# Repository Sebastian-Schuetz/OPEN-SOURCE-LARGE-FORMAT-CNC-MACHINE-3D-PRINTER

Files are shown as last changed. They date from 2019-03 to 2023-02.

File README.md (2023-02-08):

# Open-source-Large-CNC

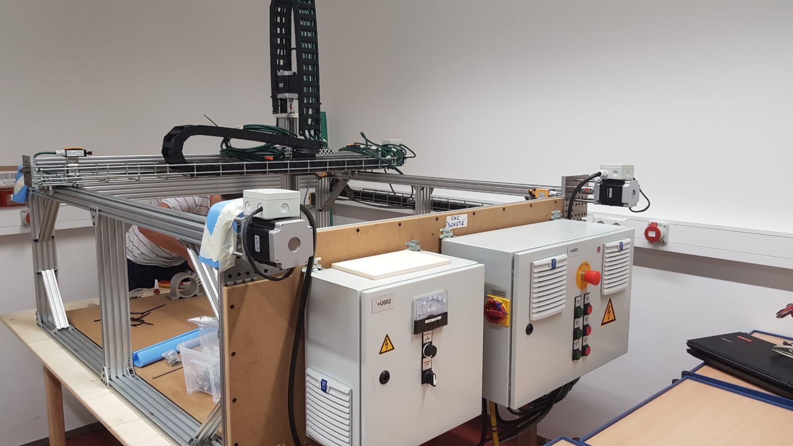
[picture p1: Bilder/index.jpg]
A picture of the finished CNC The finished CNC-machine


In this Github-Repo you can find the Documentation and CAD files for a large format CNC-machine we build with OpenBuilds parts.
This build was also published in the OpenBuilds-Forum: https://openbuilds.com/threads/open-source-large-format-cnc-machine-and-3d-printer.13904/
and on our blog: https://schuetzbuilds.de/open-source-large-format-cnc-machine-and-3d-printer

The total size of the machine is roughly:
-	X: 172 cm
-	Y: 172 cm
-	Z: 128 cm
and weights around 200 kg.

For further information you should take a look in the CNC-OpenBuilds.pdf file! 

Filestructure:

- Bilder: contains (additional) pictures to those in the pdf
- CAD-files: contains CAD-files (who would have thought). Furthermore you can check out the online model here: http://a360.co/2y7nwAO 
- Motormounts-dxf: The 3D-DXF files for the motor mounts, so that you don´t have to extract them form the CAD-model for milling
- Aufbauanleitung.pdf: Contains the "manual" on how to build the CNC. For reference always stick to the CAD.
- CNC-Mill-v3_Render.jpg: A high quality render of the finished machine
- CNC-OpenBuilds.pdf: THE MOST IMPORTANT DOCUMENT. It provides you with further information on the design decisions, ...
- SLP...: The circuit diagram. IT IS 28 PAGES. And was done professionaly. So if you think about building a CNC-machine and want to do it right, this is a great starting point.
- Materialliste.xlsx: The partlist with BOM

As you can see we are still missing some parts for the second y-axis.

# Team
- David Koch
- Sebastian Schütz
- Stefan Schütz

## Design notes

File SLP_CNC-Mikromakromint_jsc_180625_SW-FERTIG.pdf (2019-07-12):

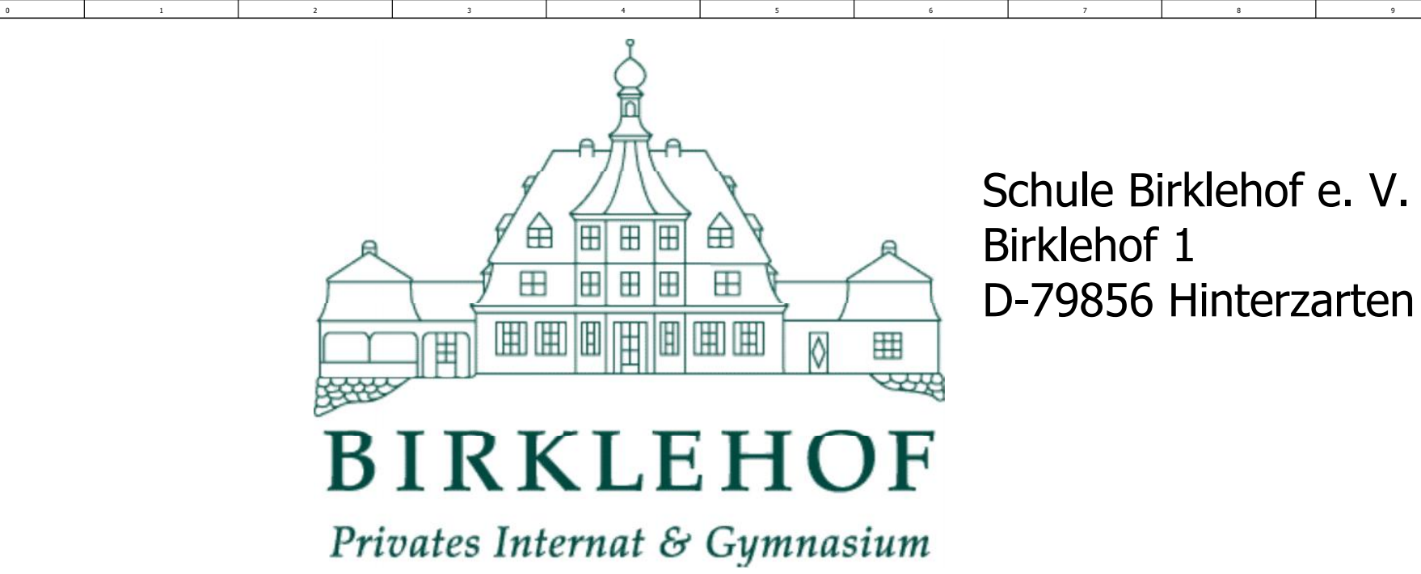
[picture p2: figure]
Schule Birklehof e. V. Birklehof 1 D-79856 Hinterzarten
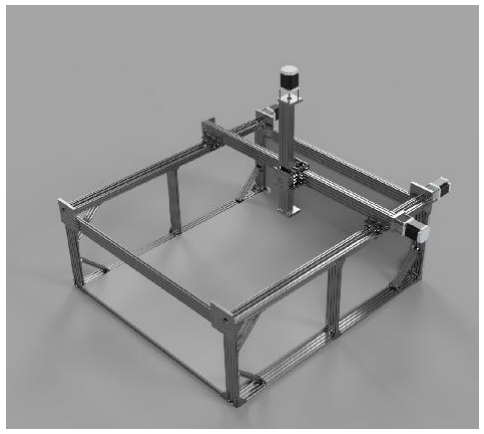
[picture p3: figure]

| | | | 31.01.2018 | 2017/18 CNC-3D-Portalfräse | | Deckblatt | Zeichnungsnummer CNC17-01 | =
| | | Bearb. | schuetz.j | | | | | +
| | | Gepr | | | | | | | Blatt
Änderung | Datum | Name | Urspr | | Ersatz von | Ersetzt durch

&EDA/3

# CNC-3D-Portalfräse

# CNC17-01

# ELEKTRODOKUMENTATION

2017/18

# Projekt: Baujahr:

# Projekt Nr.:

&EDA/4

Urspr | CNC17-01

## Inhaltsverzeichnis

&EDB/3

25.06.2018
Zeichnungsnummer | -600

Fabrik-Nr.

C:\Users\schuetz.j\Daten\Eplan_Prj\CNC-Portalfräse_Mikromakromint.edb\Images\Brunnhuber.jpg | CNC17-01
Seite | Seitenbeschreibung | Seitenzusatzfeld | Datum | Bearbeiter | X
&EAA/1 | Deckblatt | | 31.01.2018 | schuetz.j | X
&EDA/3 | Igus Kette 1+2 | | 12.02.2018 | schuetz.j
&EDA/4 | Igus Kette 3 | | 12.02.2018 | schuetz.j
&EAB/2 | Inhaltsverzeichnis | | 25.06.2018 | schuetz.j
&EDB/3 | Allgemeine Info | | 31.01.2018 | schuetz.j
&EDB/4 | Betriebsmittelkennzeichnung | | 08.02.2018 | schuetz.j
&EFS+U001/1 | Einspeisung | | 22.05.2018 | schuetz.j
&EFS+U001/2 | Steuerung Allgemein | | 22.05.2018 | schuetz.j
&EFS+U001/3 | Steuerung Arduino | | 30.05.2018 | schuetz.j
&EFS+U001/3.a | Arduino Pinout | | 20.02.2018 | schuetz.j
&EFS+U001/4 | Optokoppler - Endschalter | | 25.06.2018 | schuetz.j
&EFS+U001/5 | Optokoppler - Motortreiber | | 25.06.2018 | schuetz.j
&EFS+U001/6 | Leistung X-Achse | | 25.06.2018 | schuetz.j
&EFS+U001/7 | Leistung Y-Achse | | 30.05.2018 | schuetz.j
&EFS+U001/8 | Leistung Z-Achse | | 25.06.2018 | schuetz.j
&EFS+U001/9 | Extruder (optional) | | 25.06.2018 | schuetz.j
&EFS+U002/10 | Frequenzumrichter Spindel | | 22.05.2018 | schuetz.j
&EMB2/24 | Kabelübersicht : =-W0 - =-W504 | | 25.06.2018 | schuetz.j
&EMA1/15 | Klemmenplan +U001-X0 | | 30.05.2018 | schuetz.j
&EMA1/16 | Klemmenplan +U001-X1 | | 25.06.2018 | schuetz.j
&EMA1/17 | Klemmenplan +U001-X2 | | 30.05.2018 | schuetz.j
&EMA1/18 | Klemmenplan +U001-X3 | | 30.05.2018 | schuetz.j
&EMA1/19 | Klemmenplan +U001-X4 | | 25.06.2018 | schuetz.j
&EMA1/20 | Klemmenplan +U001-X4 | | 30.05.2018 | schuetz.j
&EMA1/21 | Klemmenplan +U001-X5 | | 30.05.2018 | schuetz.j
&EMA1/22 | Klemmenplan +U001-X6 | | 25.06.2018 | schuetz.j
&EMA1/23 | Klemmenplan +U002-X5 | | 30.05.2018 | schuetz.j
&EPC/25 | Artikelstückliste : - MEN.Pro Top13A | | 30.05.2018 | schuetz.j
&EPC/26 | Artikelstückliste : Pollin.250411 - Eaton.LS-11/L_#266110 | | 30.05.2018 | schuetz.j
&ETL/30 | Schaltschrankaufbau | | 28.05.2018 | schuetz.j

Spalte X: eine automatisch erzeugte Seite wurde manuell nachbearbeitet

# Inhaltsverzeichnis

F06_001

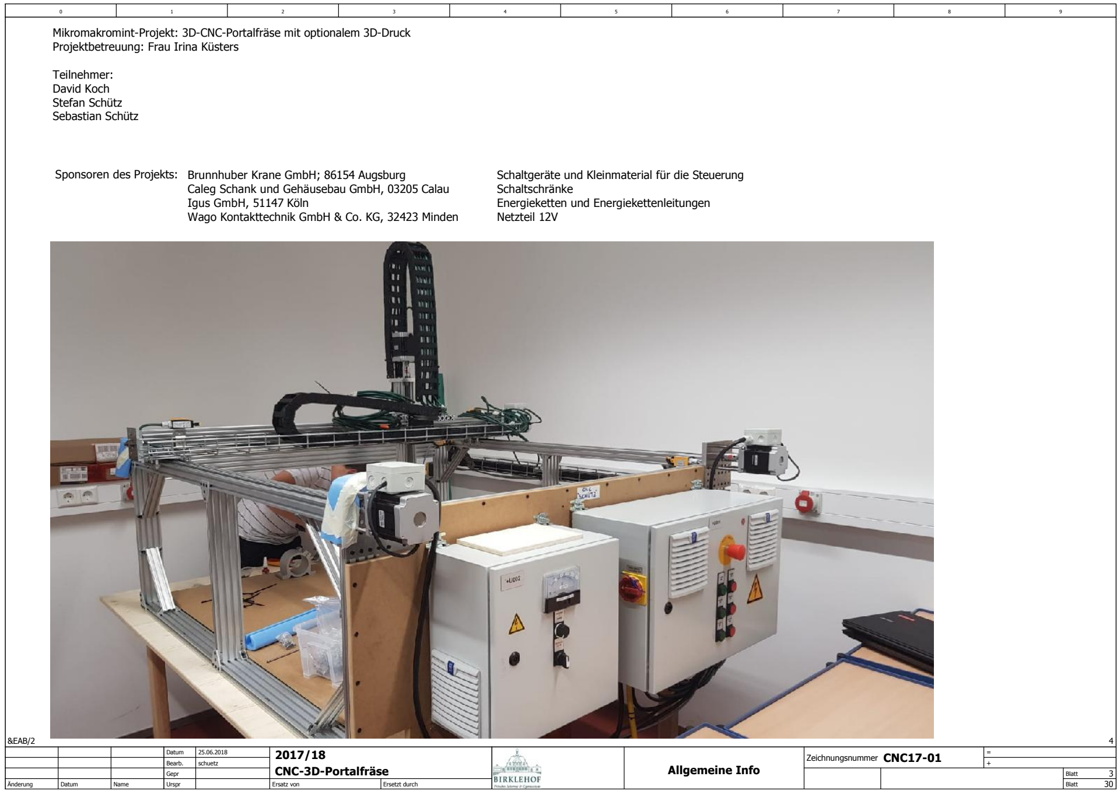
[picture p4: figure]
&EAB/2; schuetz; Allgemeine Info; Projektbetreuung: Frau Irina Küsters; Teilnehmer: David Koch Stefan Schütz Sebastian Schütz; Igus GmbH, 51147 Köln; Schaltschränke; Netzteil 12V

## Mikromakromint-Projekt: 3D-CNC-Portalfräse mit optionalem 3D-Druck

## Sponsoren des Projekts: Brunnhuber Krane GmbH; 86154 Augsburg Caleg Schank und Gehäusebau GmbH, 03205 Calau

## Wago Kontakttechnik GmbH & Co. KG, 32423 Minden

## Schaltgeräte und Kleinmaterial für die Steuerung

## Energieketten und Energiekettenleitungen

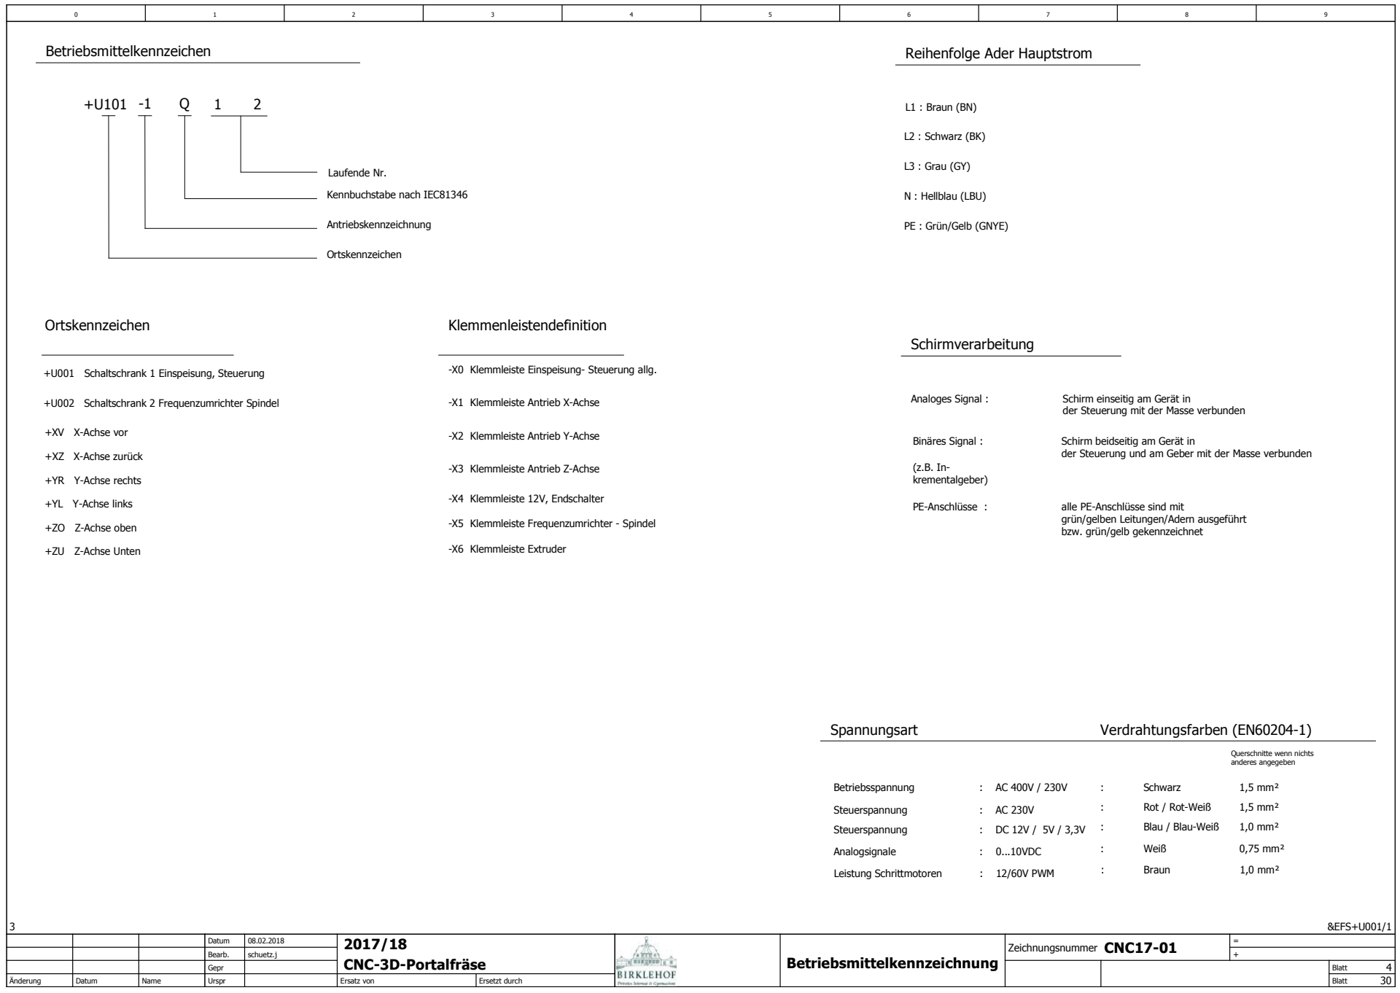
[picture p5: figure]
Betriebsmittelkennzeichnung; &EFS+U001/1; Betriebsmittelkennzeichen; Ortskennzeichen; Kennbuchstabe nach IEC81346; Klemmenleistendefinition; Antriebskennzeichnung; -X2 Klemmleiste Antrieb Y-Achse; -X3 Klemmleiste Antrieb Z-Achse; -X1 Klemmleiste Antrieb X-Achse; -X4 Klemmleiste 12V, Endschalter; Laufende Nr.; +XV X-Achse vor; +XZ X-Achse zurück; +YR Y-Achse rechts; +YL Y-Achse links; +ZO Z-Achse oben; +ZU Z-Achse Unten; -X6 Klemmleiste Extruder; Reihenfolge Ader Hauptstrom; L1 : Braun (BN); L2 : Schwarz (BK); L3 : Grau (GY); N : Hellblau (LBU); Schirmverarbeitung; Analoges Signal :; Binäres Signal :; (z.B. In- krementalgeber); PE-Anschlüsse :; Schirm einseitig am Gerät in der Steuerung mit der Masse verbunden; Schirm beidseitig am Gerät in; alle PE-Anschlüsse sind mit grün/gelben Leitungen/Adern ausgeführt bzw. grün/gelb gekennzeichnet; PE : Grün/Gelb (GNYE); Betriebsspannung; Steuerspannung; Querschnitte wenn nichts anderes angegeben; Schwarz; Rot / Rot-Weiß; Blau / Blau-Weiß; 1,5 mm²; 1,0 mm²

-X0 Klemmleiste Einspeisung- Steuerung allg. +U001 Schaltschrank 1 Einspeisung, Steuerung

+U002 Schaltschrank 2 Frequenzumrichter Spindel

-X5 Klemmleiste Frequenzumrichter - Spindel der Steuerung und am Geber mit der Masse verbunden

Spannungsart | Verdrahtungsfarben (EN60204-1)
Analogsignale | : | Weiß | 0,75 mm² : 0...10VDC
Leistung Schrittmotoren | : | Braun | 1,0 mm² : 12/60V PWM

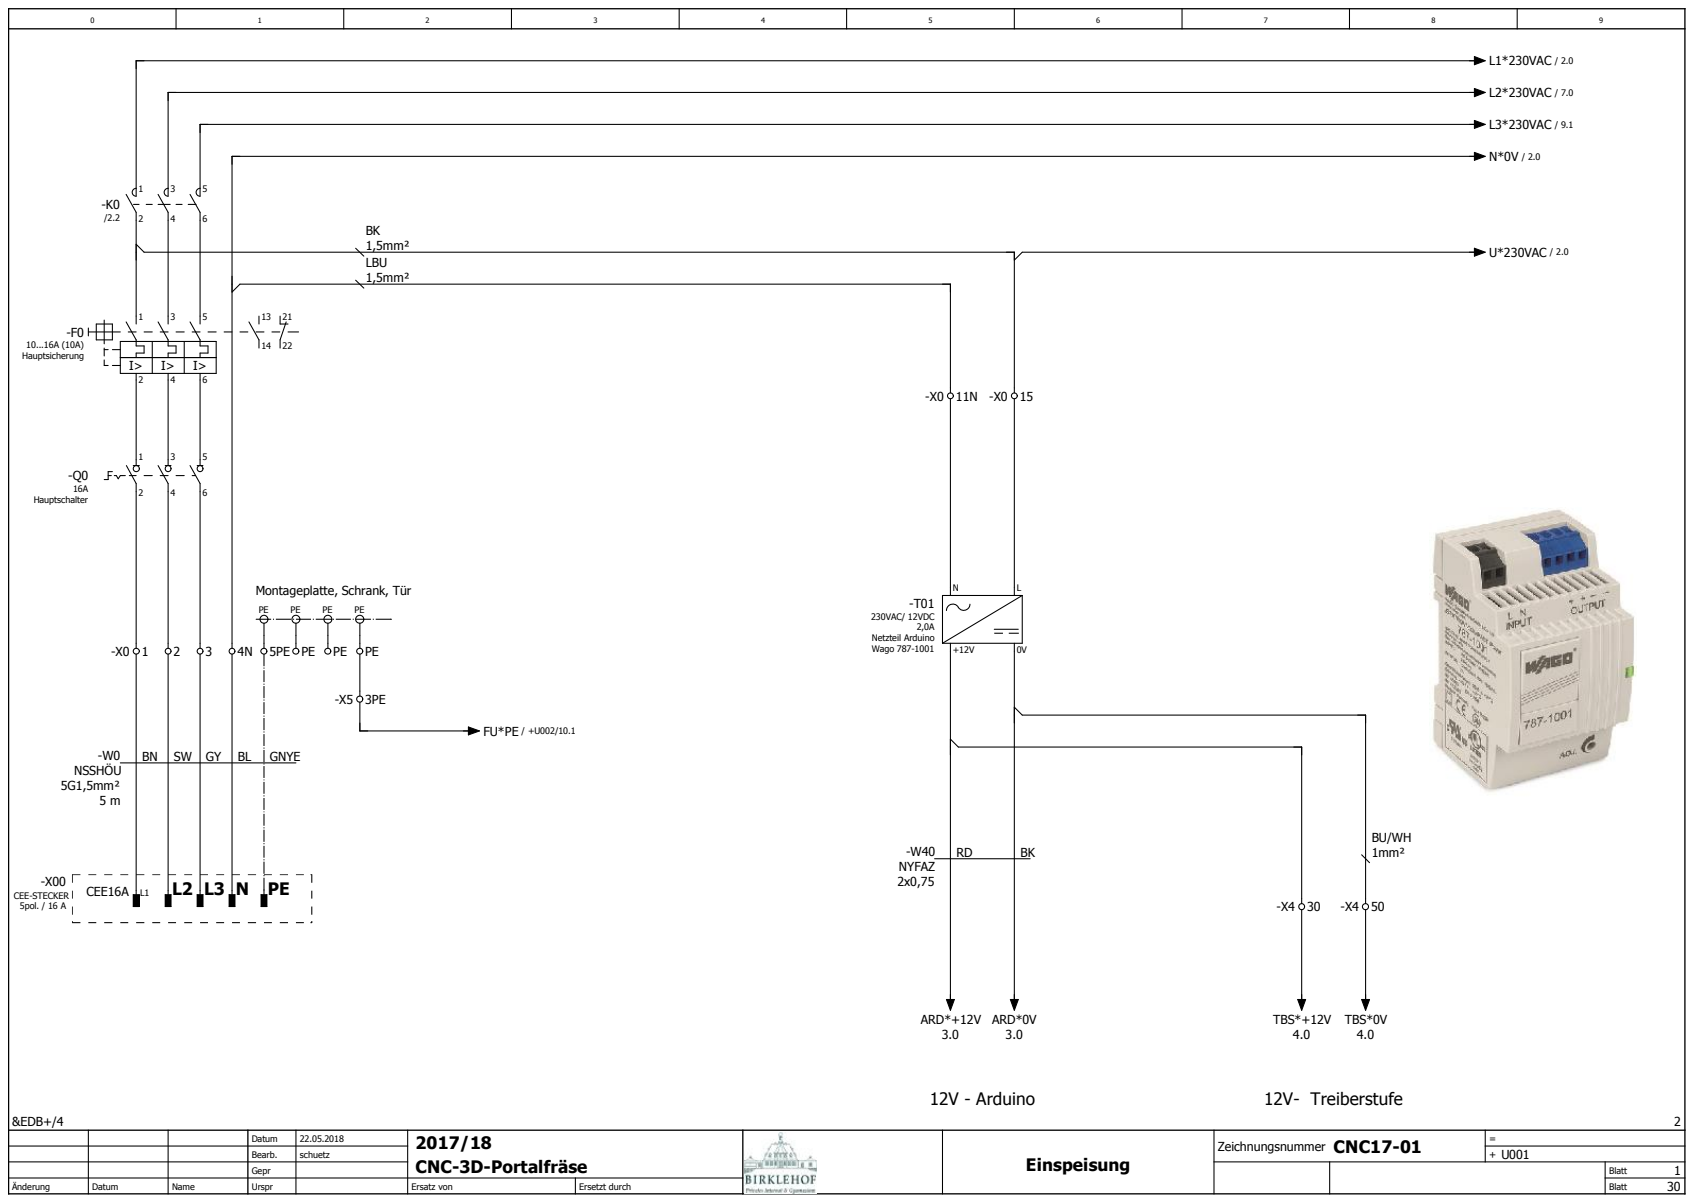
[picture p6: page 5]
&EDB+/4; U001 Einspeisung; 12V - Arduino; 12V- Treiberstufe; -Q0 16A Hauptschalter; -F0 10...16A (10A) Hauptsicherung; CEE16A L1; CEE-STECKER 5pol. / 16 A; NSSHÖU 5G1,5mm² 5 m; BL GNYE; -T01 230VAC/ 12VDC 2,0A Netzteil Arduino Wago 787-1001; 1mm²; 1,5mm²; LBU; -W40 NYFAZ 2x0,75; ARD*+12V 3.0; ARD*0V 3.0; L2*230VAC / 7.0; L1*230VAC / 2.0; L3*230VAC / 9.1; U*230VAC / 2.0; TBS*+12V 4.0; TBS*0V 4.0

Montageplatte, Schrank, Tür

22.05.2018
schuetz | +

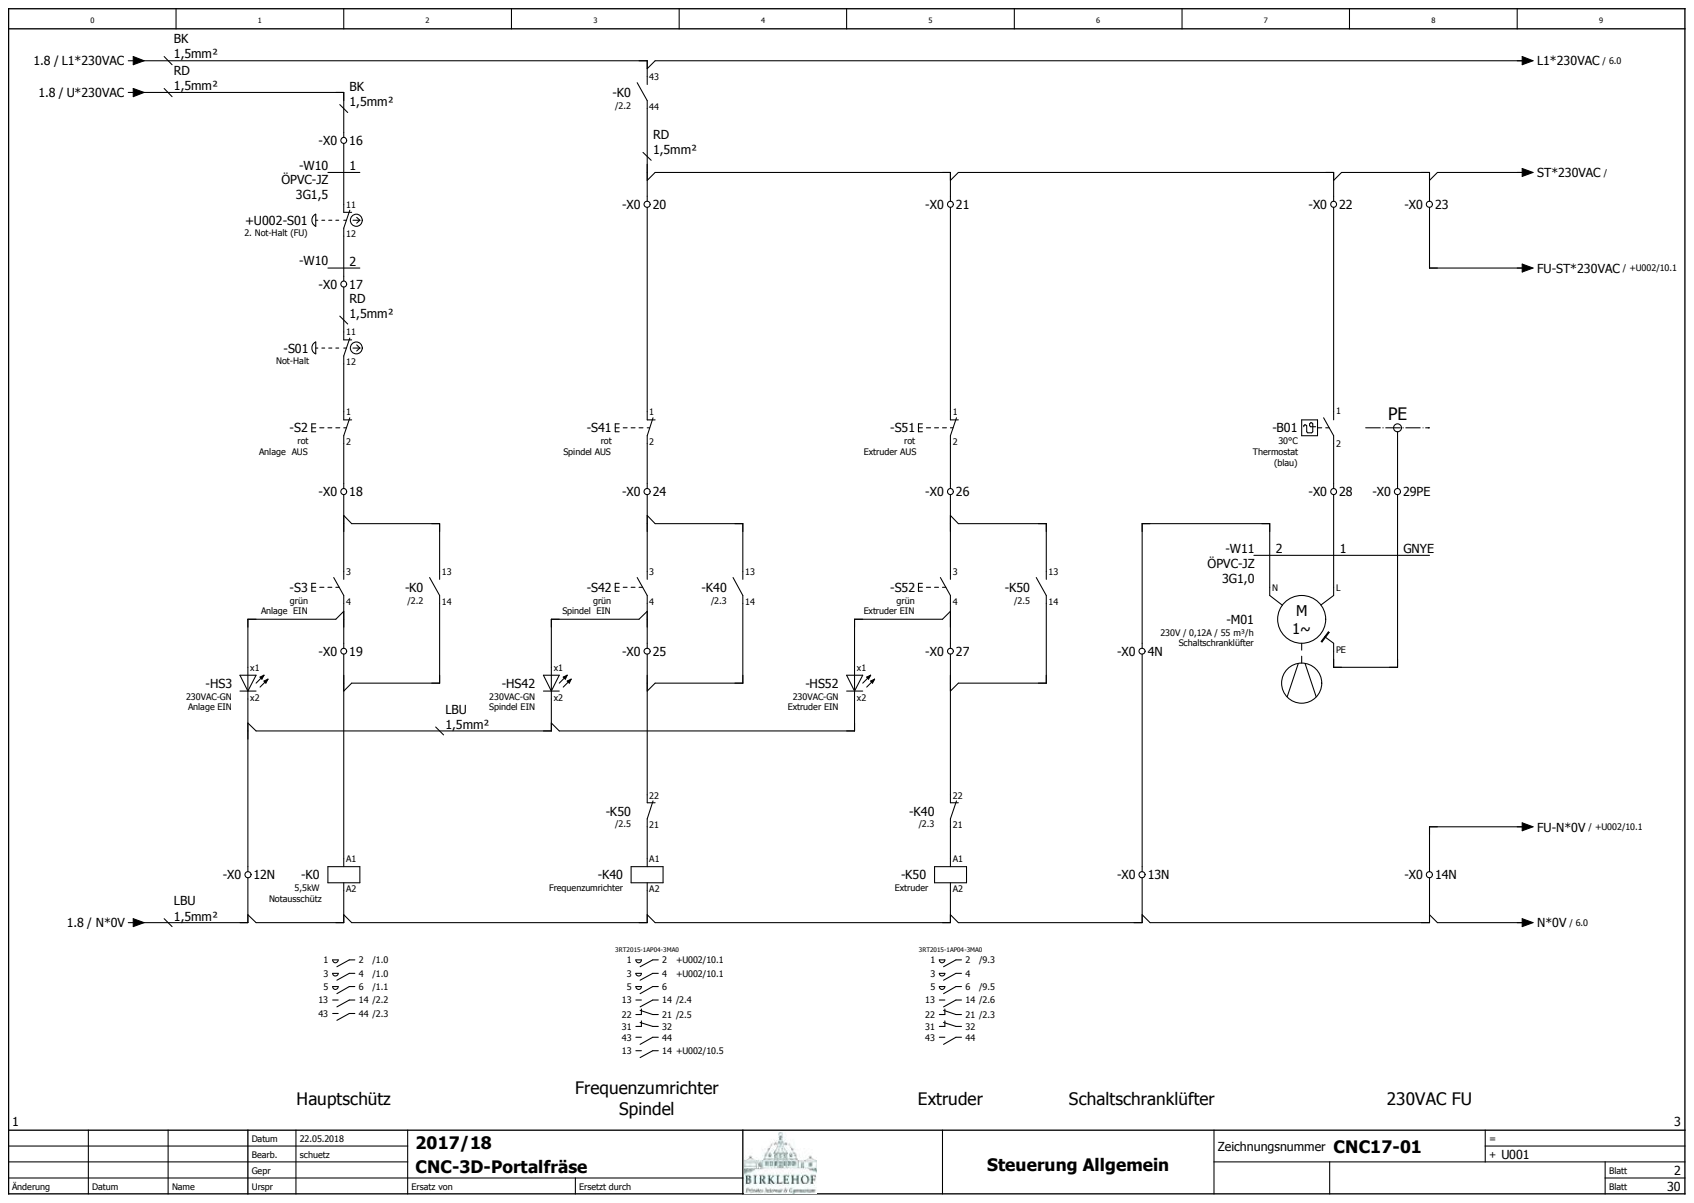
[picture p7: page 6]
U001 Steuerung Allgemein; Hauptschütz; Frequenzumrichter; Spindel; Extruder; Schaltschranklüfter; 230VAC FU; -K0 5,5kW Notausschütz; 1,5mm²; LBU; -S3 grün Anlage EIN; -S01 Not-Halt; -W10 ÖPVC-JZ 3G1,5; -S2 rot Anlage AUS; -K40 Frequenzumrichter; -S42 grün Spindel EIN; -S41 rot Spindel AUS; -K50 Extruder; -S51 rot Extruder AUS; -S52 grün Extruder EIN; -HS3 230VAC-GN Anlage EIN; -HS42 230VAC-GN Spindel EIN; -HS52 230VAC-GN Extruder EIN; -B01 30°C Thermostat (blau)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

2. Not-Halt (FU)

22.05.2018
schuetz | +

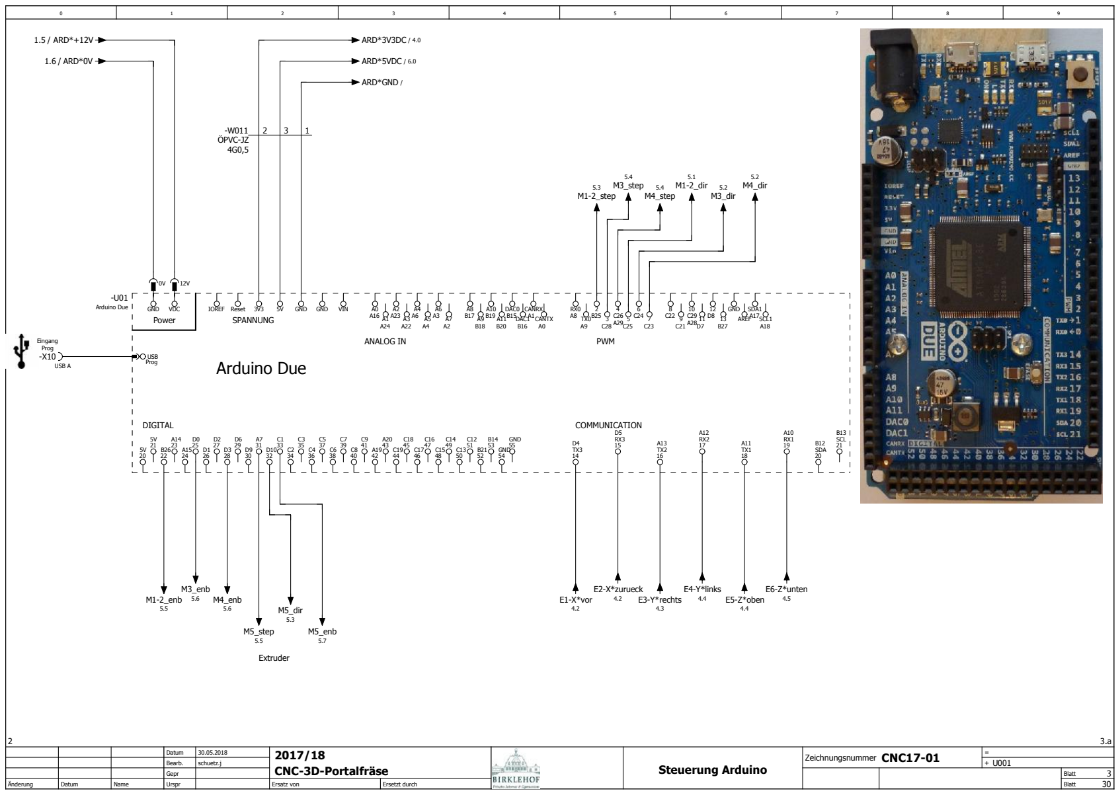
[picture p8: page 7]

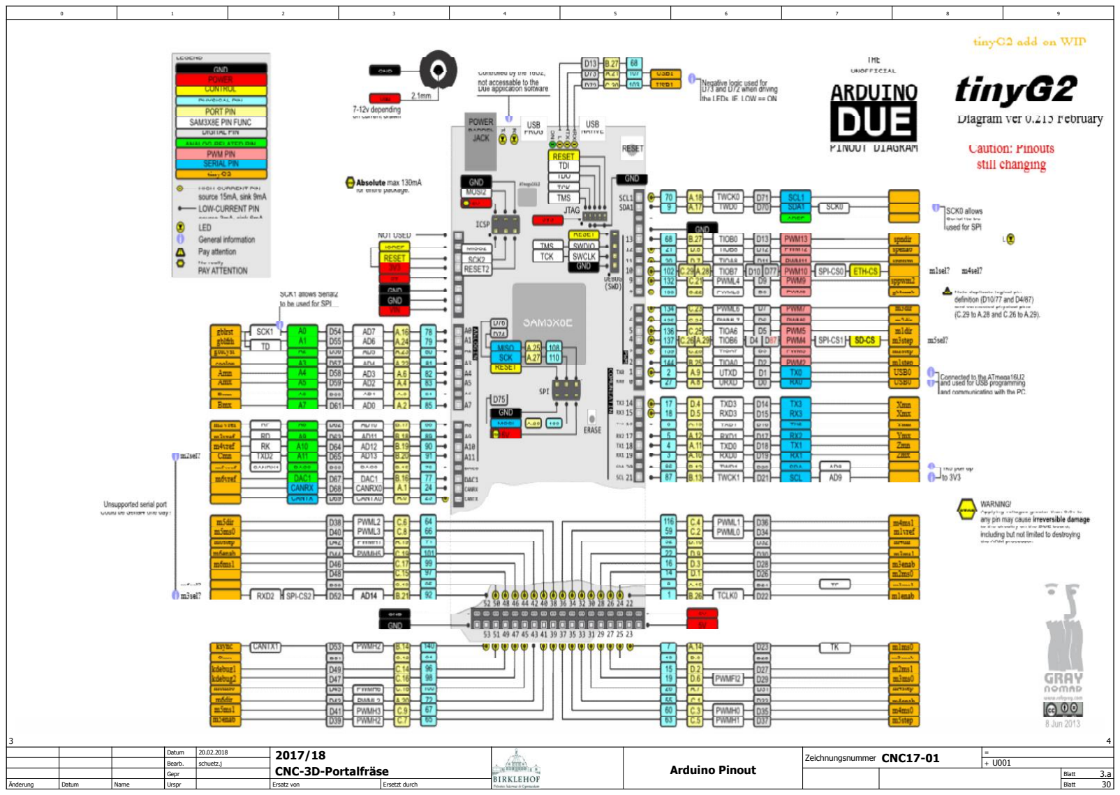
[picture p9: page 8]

## U001 Arduino Pinout

20.02.2018

3.a

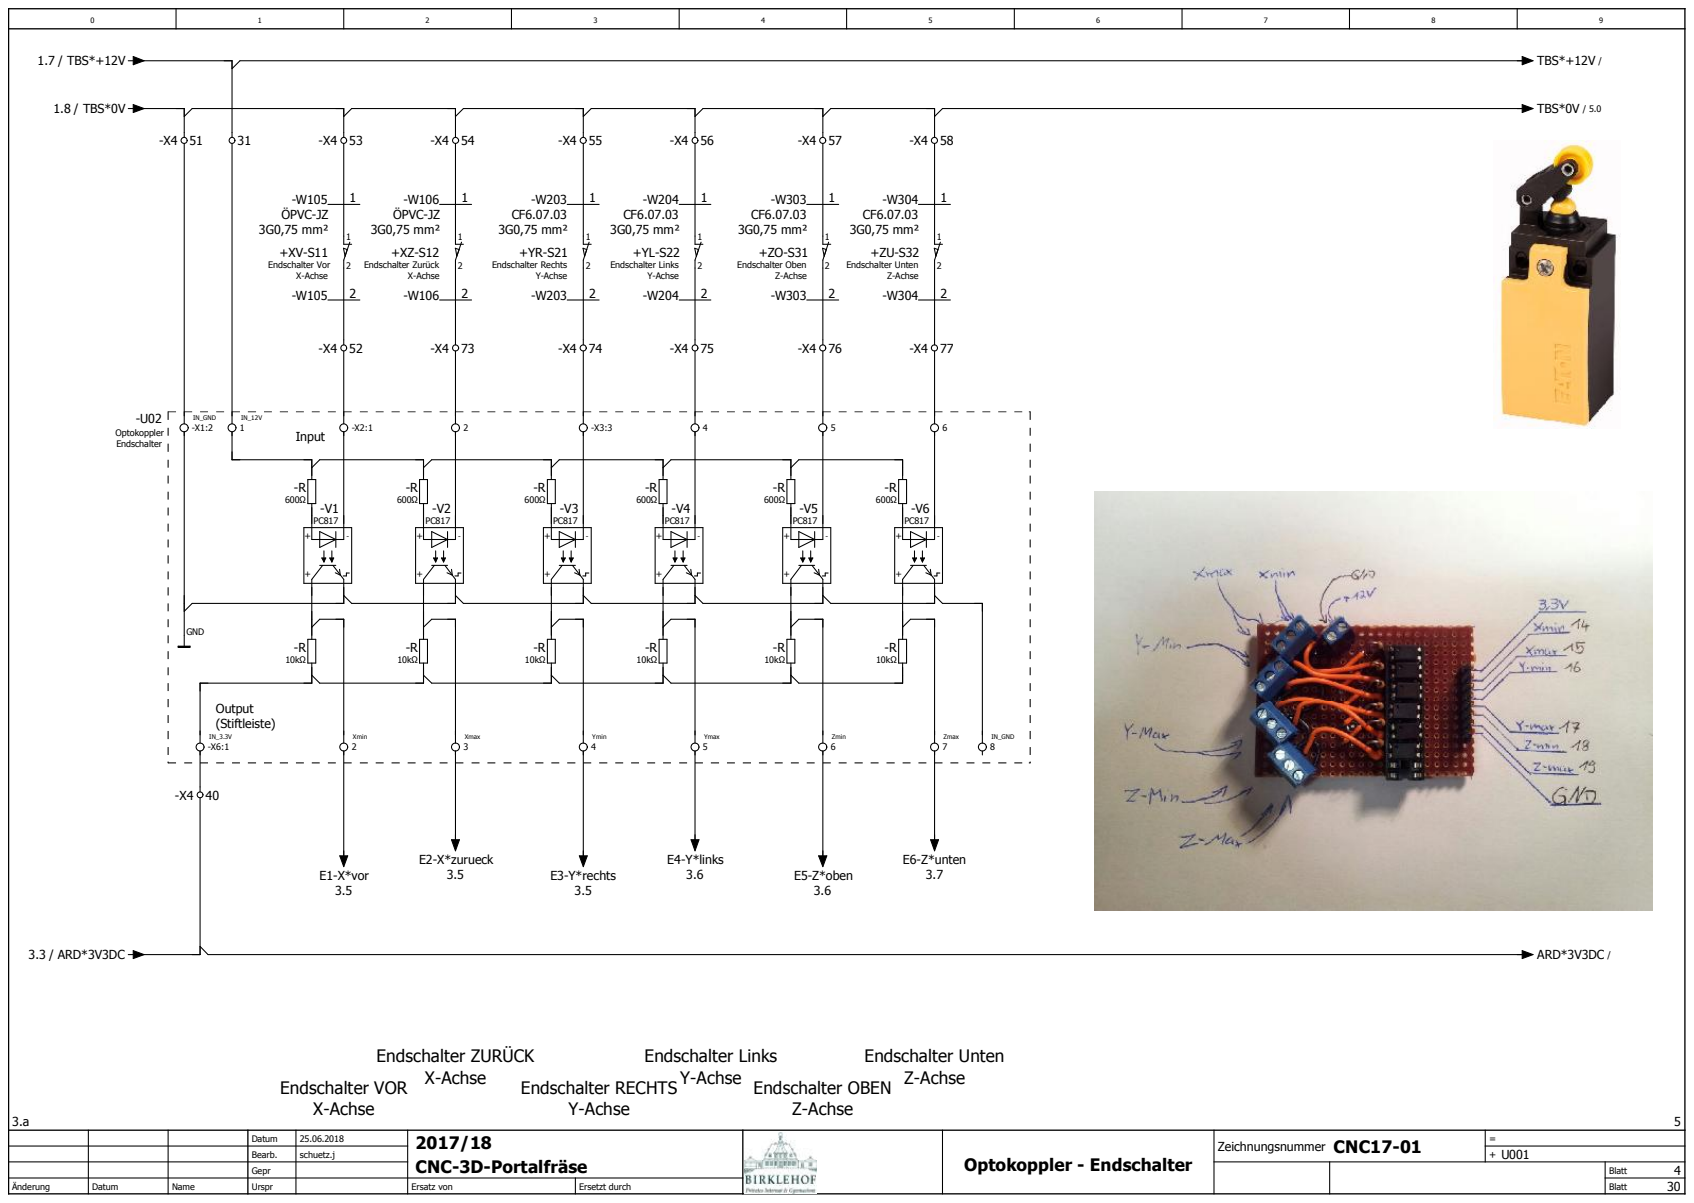
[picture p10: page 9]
U001 Optokoppler - Endschalter; Input; Output (Stiftleiste); Endschalter VOR X-Achse; Endschalter ZURÜCK; X-Achse; Endschalter RECHTS; Y-Achse; Z-Achse; Endschalter Unten Z-Achse; -U02 Optokoppler Endschalter; Xmin 2; Xmax 3; Ymin 4; Ymax 5; Zmin 6; Zmax 7; IN_GND 8; IN_GND -X1:2; GND; +XV-S11 Endschalter Vor X-Achse; -W105 ÖPVC-JZ 3G0,75 mm²; -W106 ÖPVC-JZ 3G0,75 mm² 1; +XZ-S12 Endschalter Zurück X-Achse; -W203 CF6.07.03 3G0,75 mm²; -W204 CF6.07.03 3G0,75 mm²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

Endschalter Links
Y-Achse Endschalter OBEN

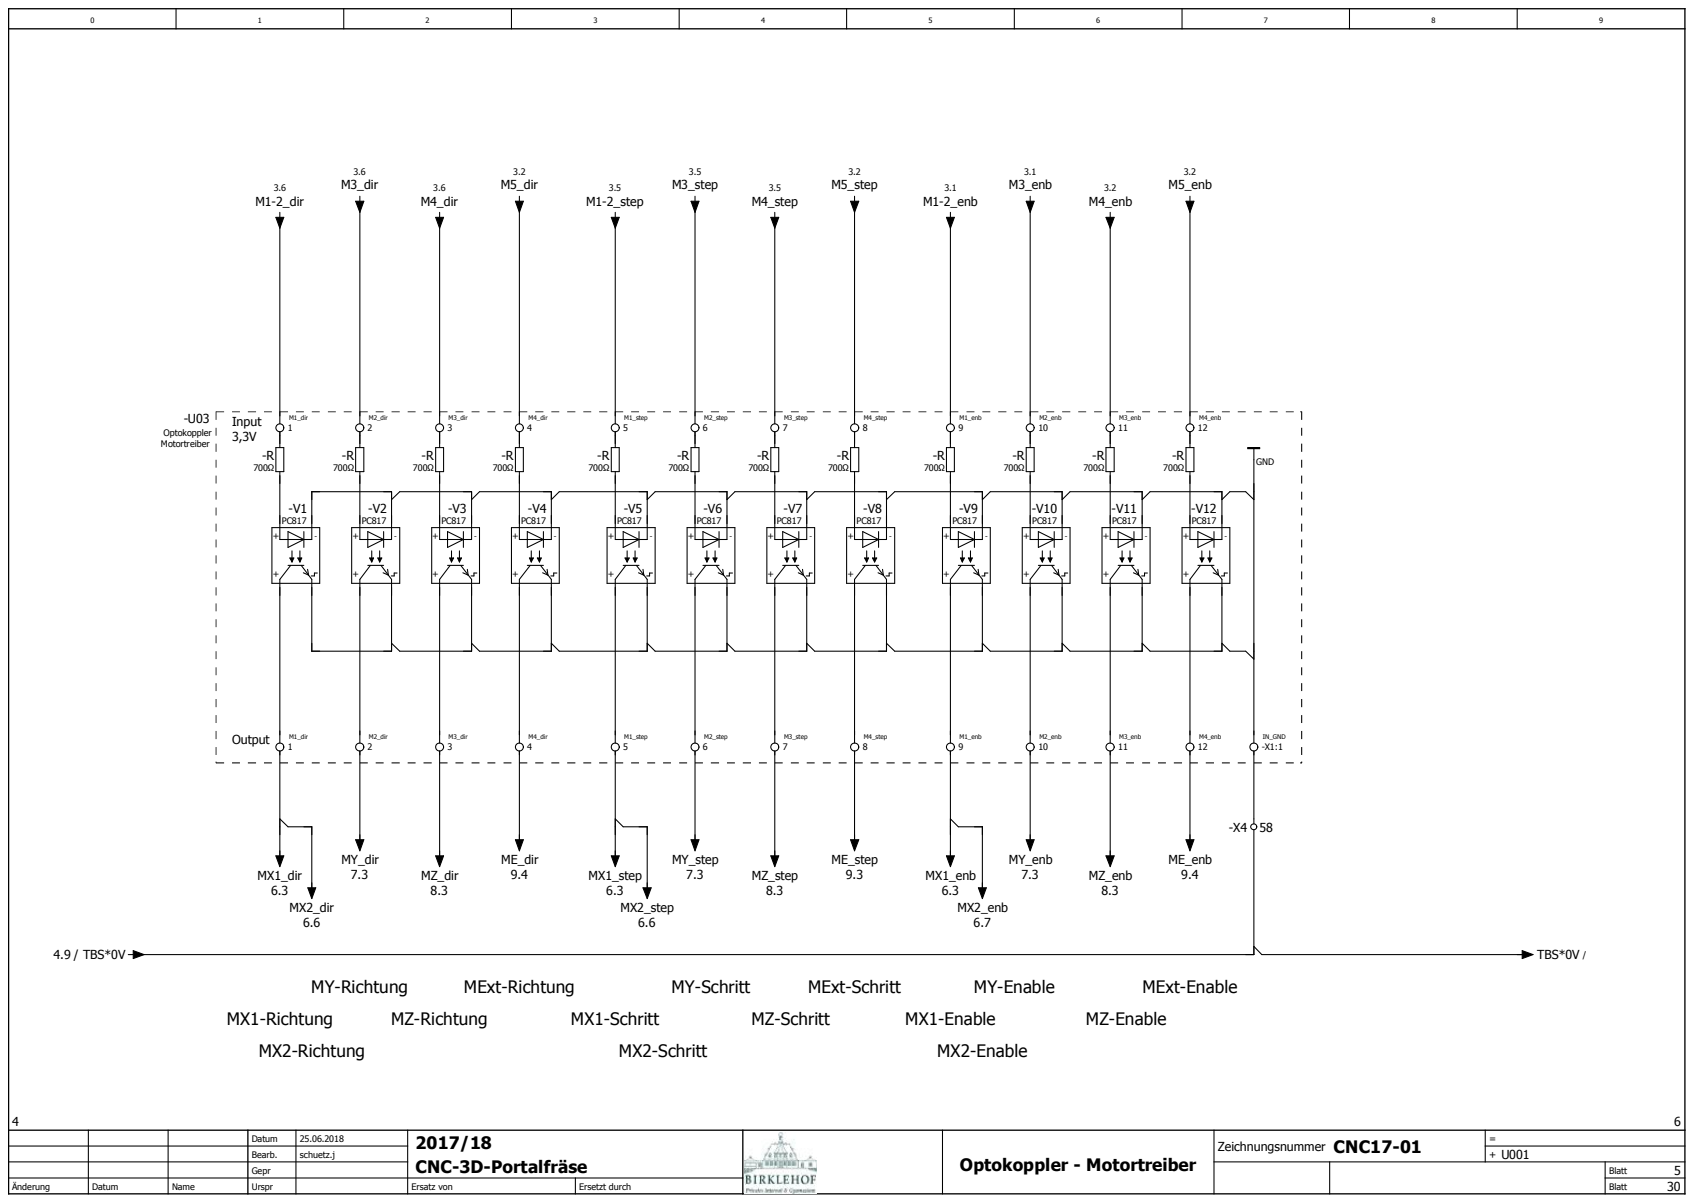
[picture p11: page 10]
U001 Optokoppler - Motortreiber; Input 3,3V; Output; MX1-Richtung; MX2-Richtung; MY-Richtung; MZ-Richtung; MX1-Schritt; MX2-Schritt; MY-Schritt; MZ-Schritt; MX1-Enable; MX2-Enable; MY-Enable; MZ-Enable; MExt-Richtung; MExt-Schritt; MExt-Enable; -U03 Optokoppler Motortreiber; M1_dir 1; M2_dir 2; M3_dir 3; M4_dir 4; IN_GND -X1:1; GND; M1_step 5; M2_step 6; M3_step 7; M4_step 8; M1_enb 9; M2_enb 10; M3_enb 11; M4_enb 12; 4.9 / TBS*0V; MX1_dir 6.3; MY_dir; MZ_dir; ME_dir 9.4; TBS*0V /; MY_step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

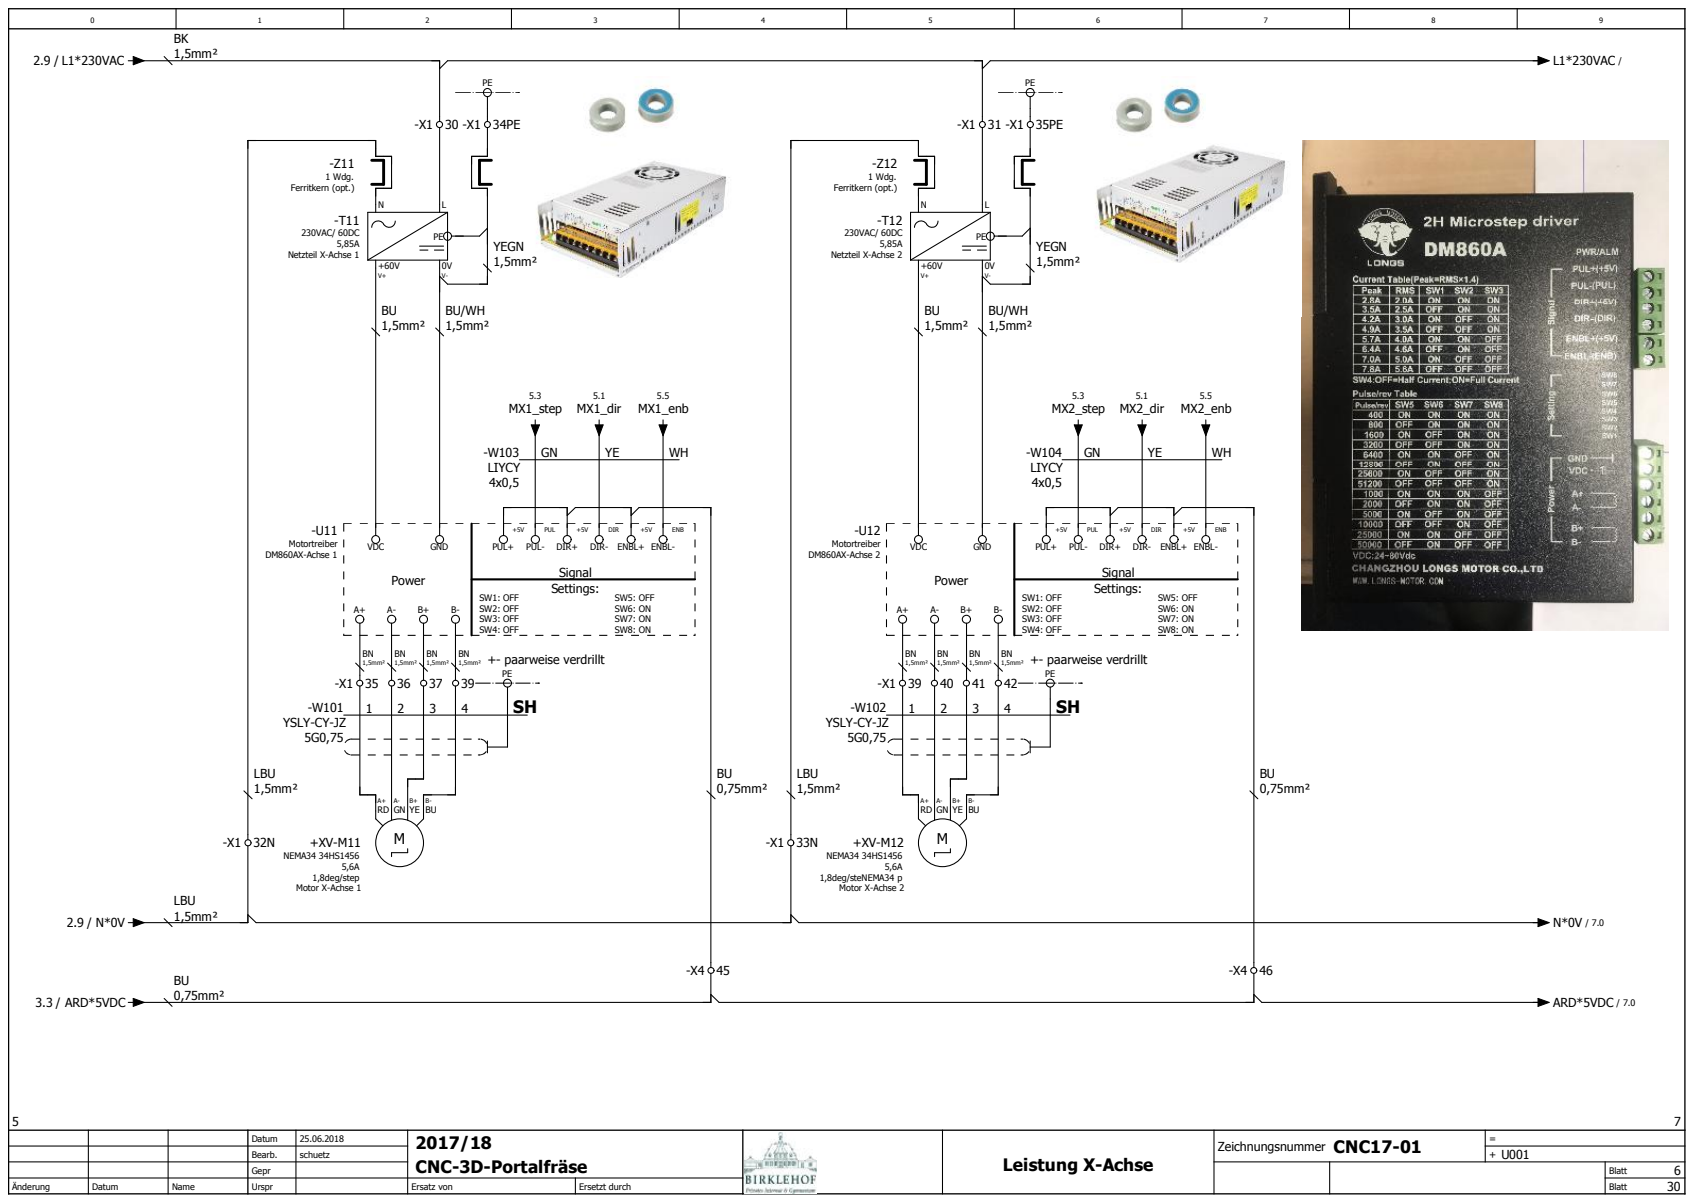
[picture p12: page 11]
schuetz; U001 Leistung X-Achse; Power; Signal; Settings:; SW1: OFF SW2: OFF SW3: OFF SW4: OFF; SW5: OFF SW6: ON SW7: ON SW8: ON; +- paarweise verdrillt; -T11 230VAC/ 60DC 5,85A Netzteil X-Achse 1; -U11 Motortreiber DM860AX-Achse 1; VDC; GND; +5V PUL+; +5V DIR+; PUL PUL-; DIR DIR-; +5V ENBL+; ENB ENBL-; 1,5mm²; LBU; +XV-M11 NEMA34 34HS1456 5,6A 1,8deg/step Motor X-Achse 1; -W101 YSLY-CY-JZ 5G0,75; -T12 230VAC/ 60DC 5,85A Netzteil X-Achse 2; -U12 Motortreiber DM860AX-Achse 2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

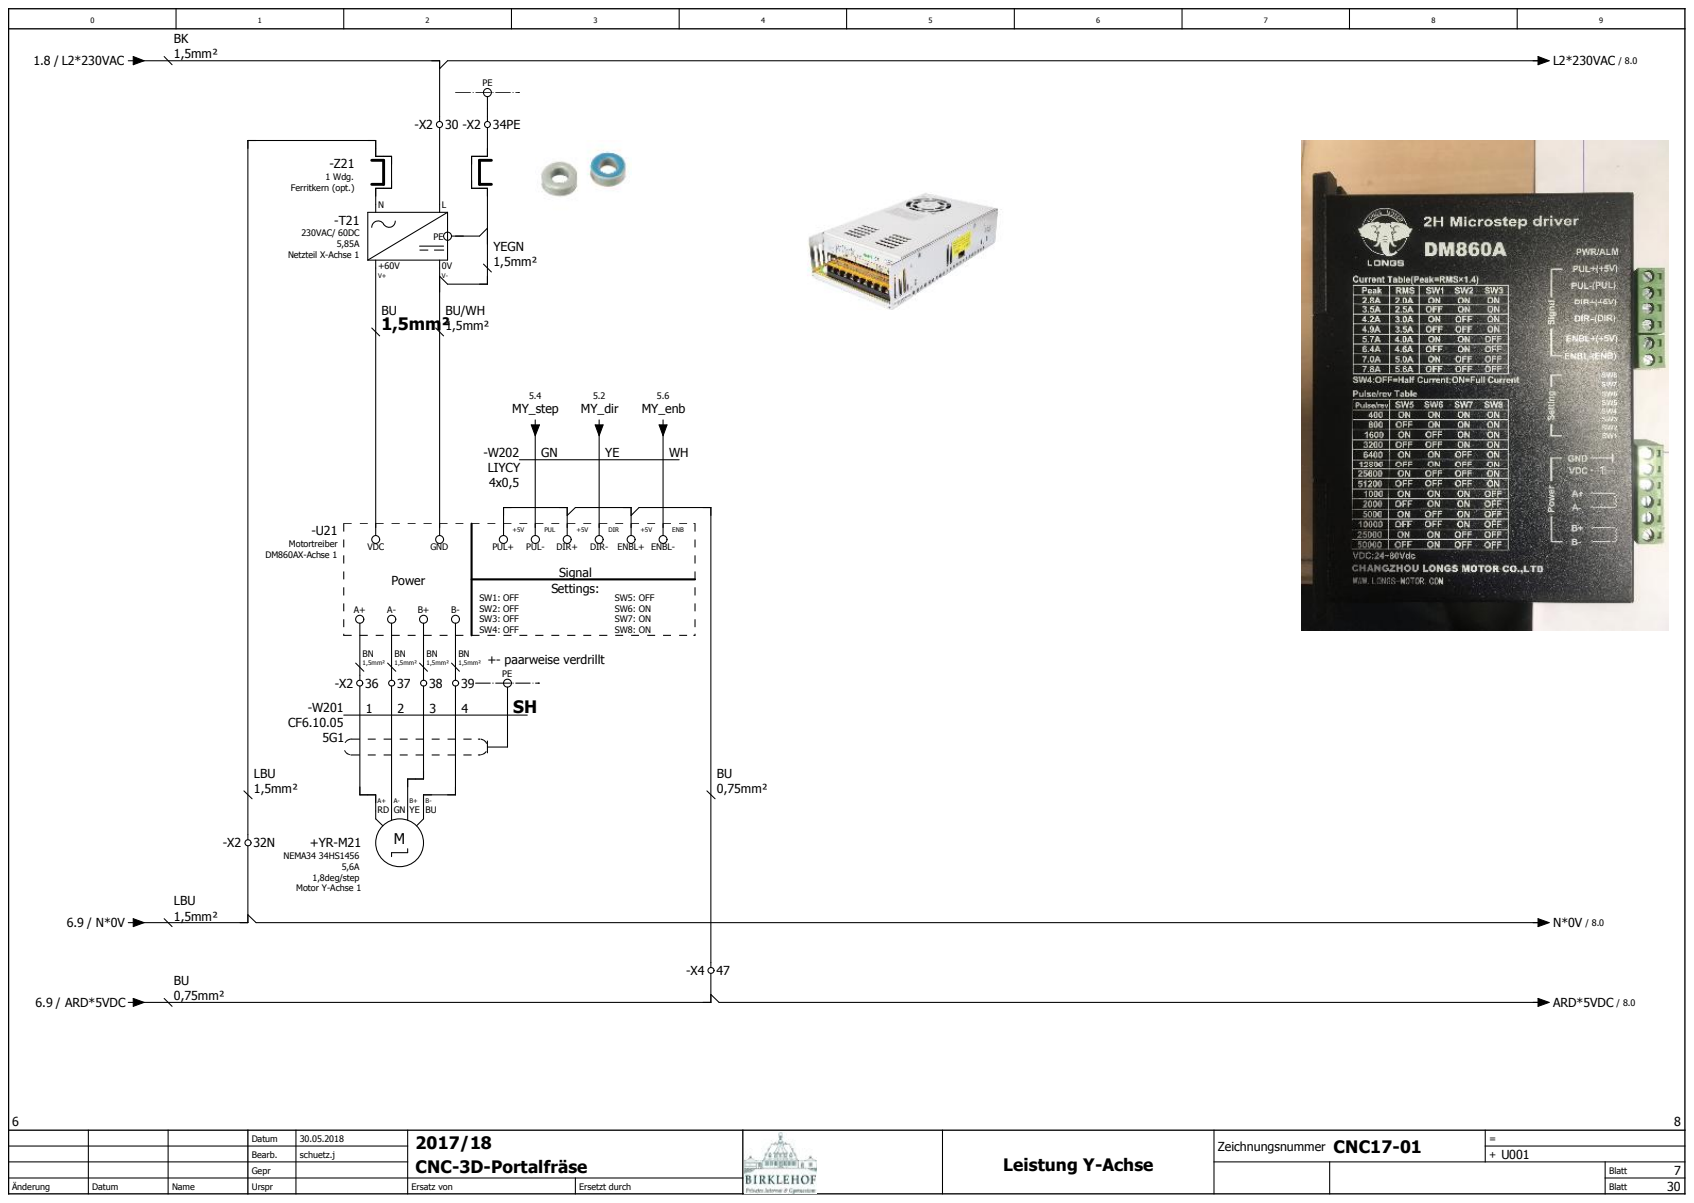
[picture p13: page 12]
U001 Leistung Y-Achse; Power; Signal; Settings:; +- paarweise verdrillt; SW1: OFF SW2: OFF SW3: OFF SW4: OFF; SW5: OFF SW6: ON SW7: ON SW8: ON; -T21 230VAC/ 60DC 5,85A Netzteil X-Achse 1; -U21 Motortreiber DM860AX-Achse 1; VDC; GND; +5V PUL+; +5V DIR+; PUL PUL-; DIR DIR-; +5V ENBL+; ENB ENBL-; 1,5mm²; LBU; +YR-M21 NEMA34 34HS1456 5,6A 1,8deg/step Motor Y-Achse 1; -Z21 1 Wdg. Ferritkern (opt.); 0,75mm²; YEGN; -W202 LIYCY 4x0,5; 1.8 / L2*230VAC; L2*230VAC / 8.0; 6.9 / ARD*5VDC; ARD*5VDC / 8.0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

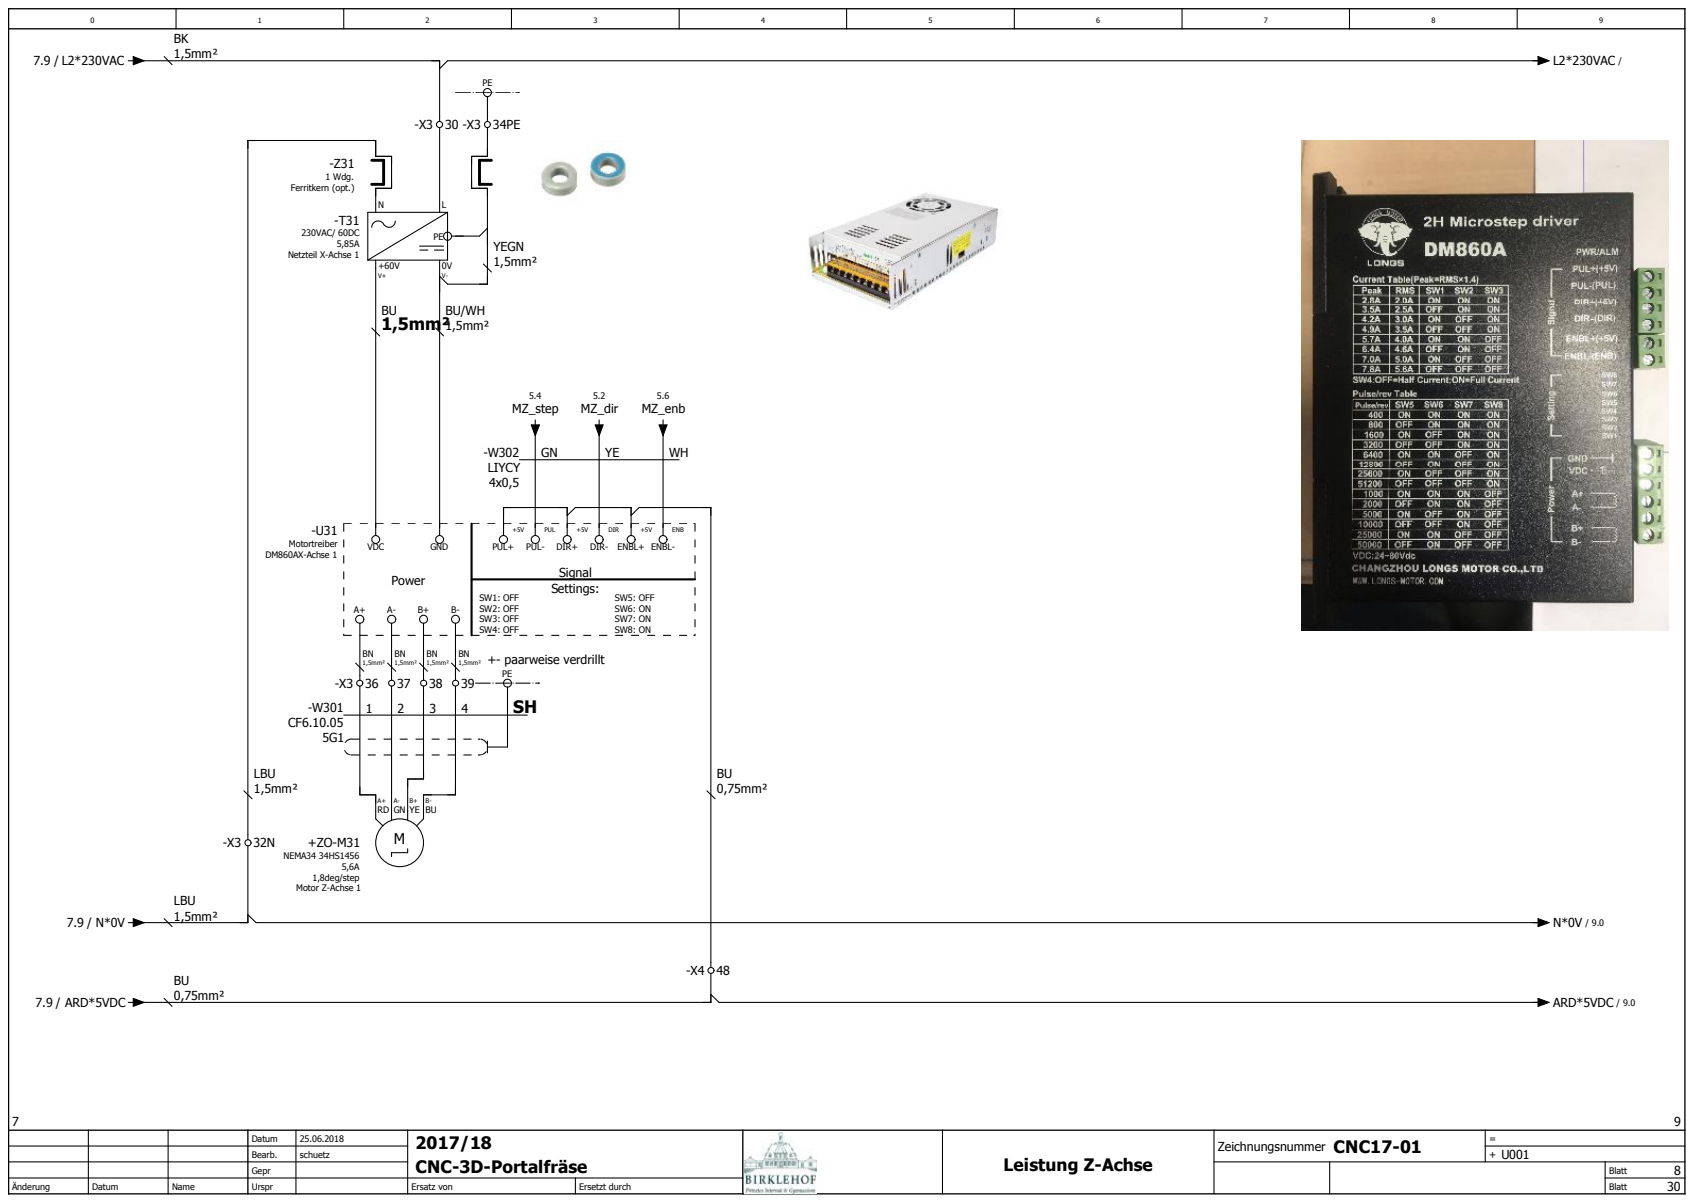
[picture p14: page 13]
schuetz; U001 Leistung Z-Achse; Power; Signal; Settings:; +- paarweise verdrillt; SW1: OFF SW2: OFF SW3: OFF SW4: OFF; SW5: OFF SW6: ON SW7: ON SW8: ON; -T31 230VAC/ 60DC 5,85A Netzteil X-Achse 1; -U31 Motortreiber DM860AX-Achse 1; VDC; GND; +5V PUL+; +5V DIR+; PUL PUL-; DIR DIR-; +5V ENBL+; ENB ENBL-; 1,5mm²; LBU; +ZO-M31 NEMA34 34HS1456 5,6A 1,8deg/step Motor Z-Achse 1; -Z31 1 Wdg. Ferritkern (opt.); 0,75mm²; YEGN; -W302 LIYCY 4x0,5; 7.9 / L2*230VAC; L2*230VAC /; 7.9 / ARD*5VDC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

# Optional vorbereitet

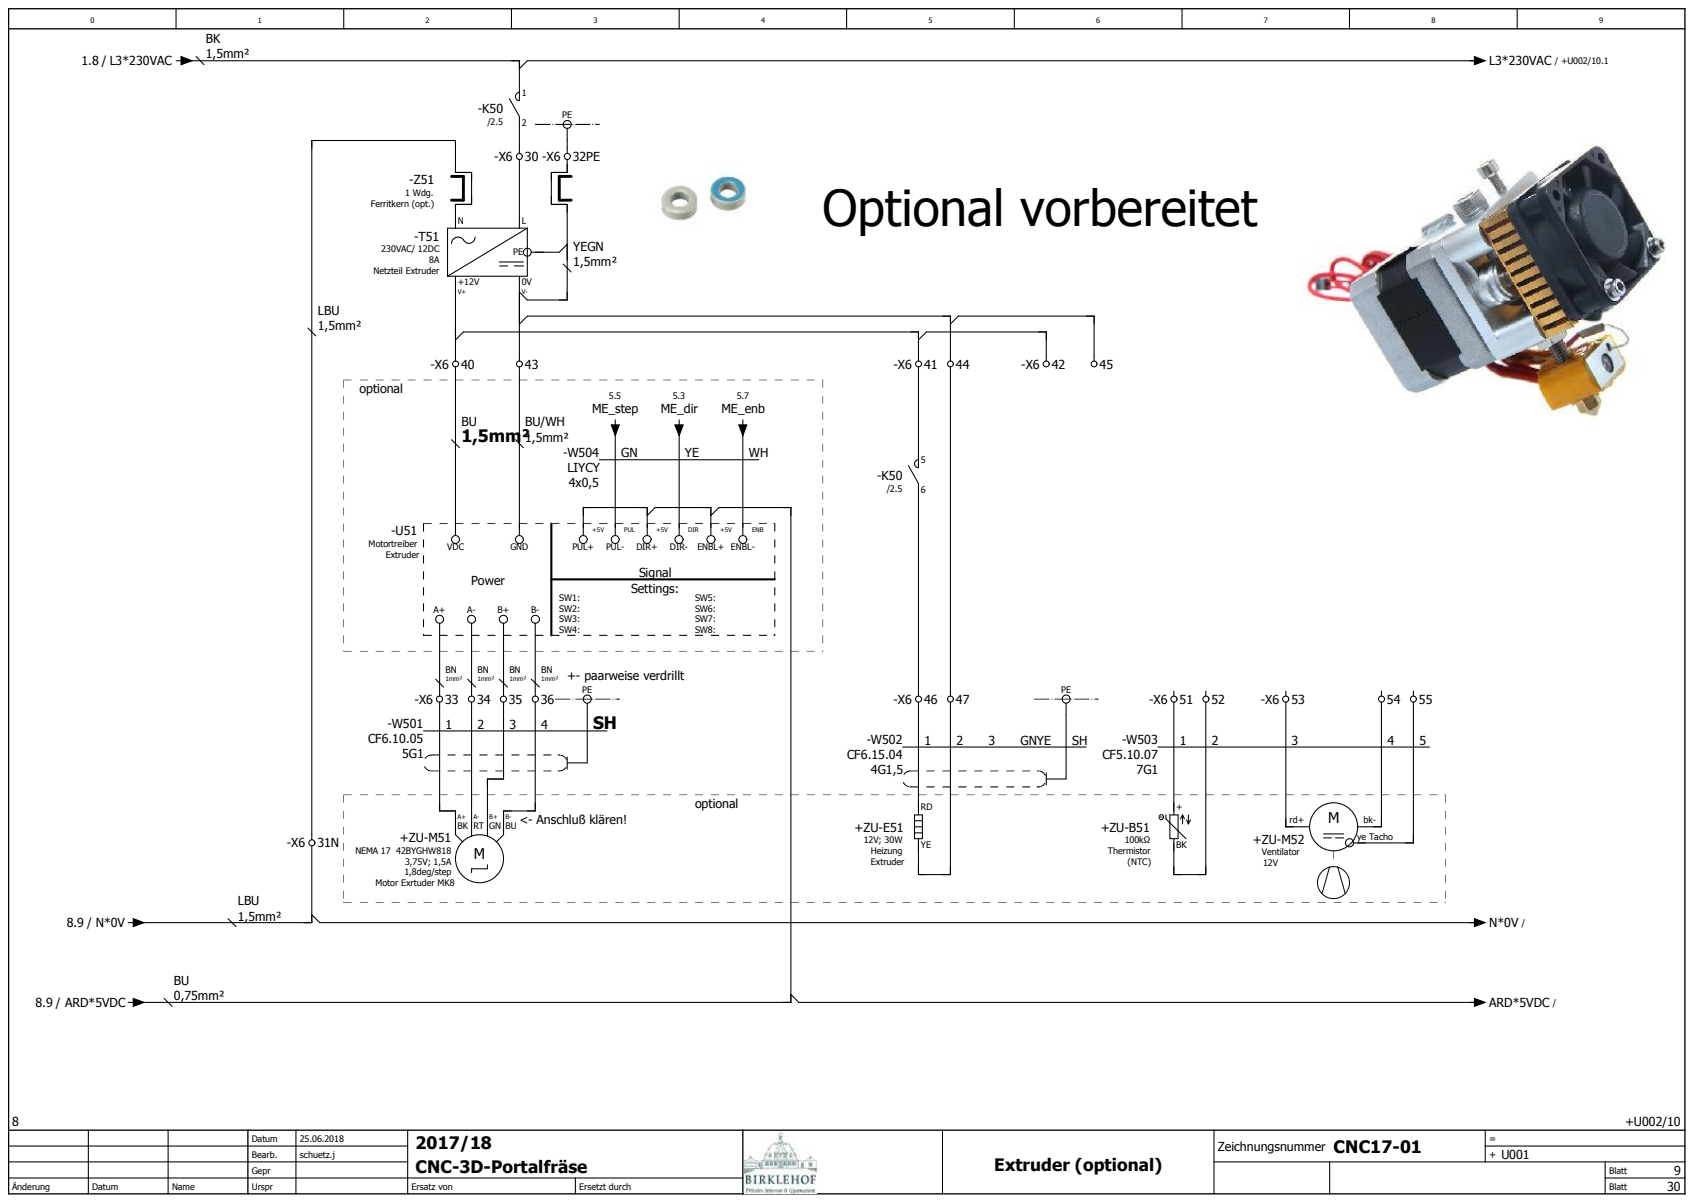
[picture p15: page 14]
U001 Extruder (optional); Power; Signal; Settings:; +- paarweise verdrillt; <- Anschluß klären!; optional; 1,5mm²; -T51 230VAC/ 12DC 8A Netzteil Extruder; -U51 Motortreiber Extruder; VDC; GND; +5V PUL+; +5V DIR+; PUL PUL-; DIR DIR-; +5V ENBL+; ENB ENBL-; LBU; +ZU-M51 NEMA 17 42BYGHW818 3,75V; 1,5A 1,8deg/step Motor Exrtuder MK8; 1mm²; +ZU-E51 12V; 30W Heizung Extruder; +ZU-B51 100k Thermistor (NTC); GNYE; -Z51 1 Wdg. Ferritkern (opt.); +ZU-M52 Ventilator; ye Tacho; YEGN; 0,75mm²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

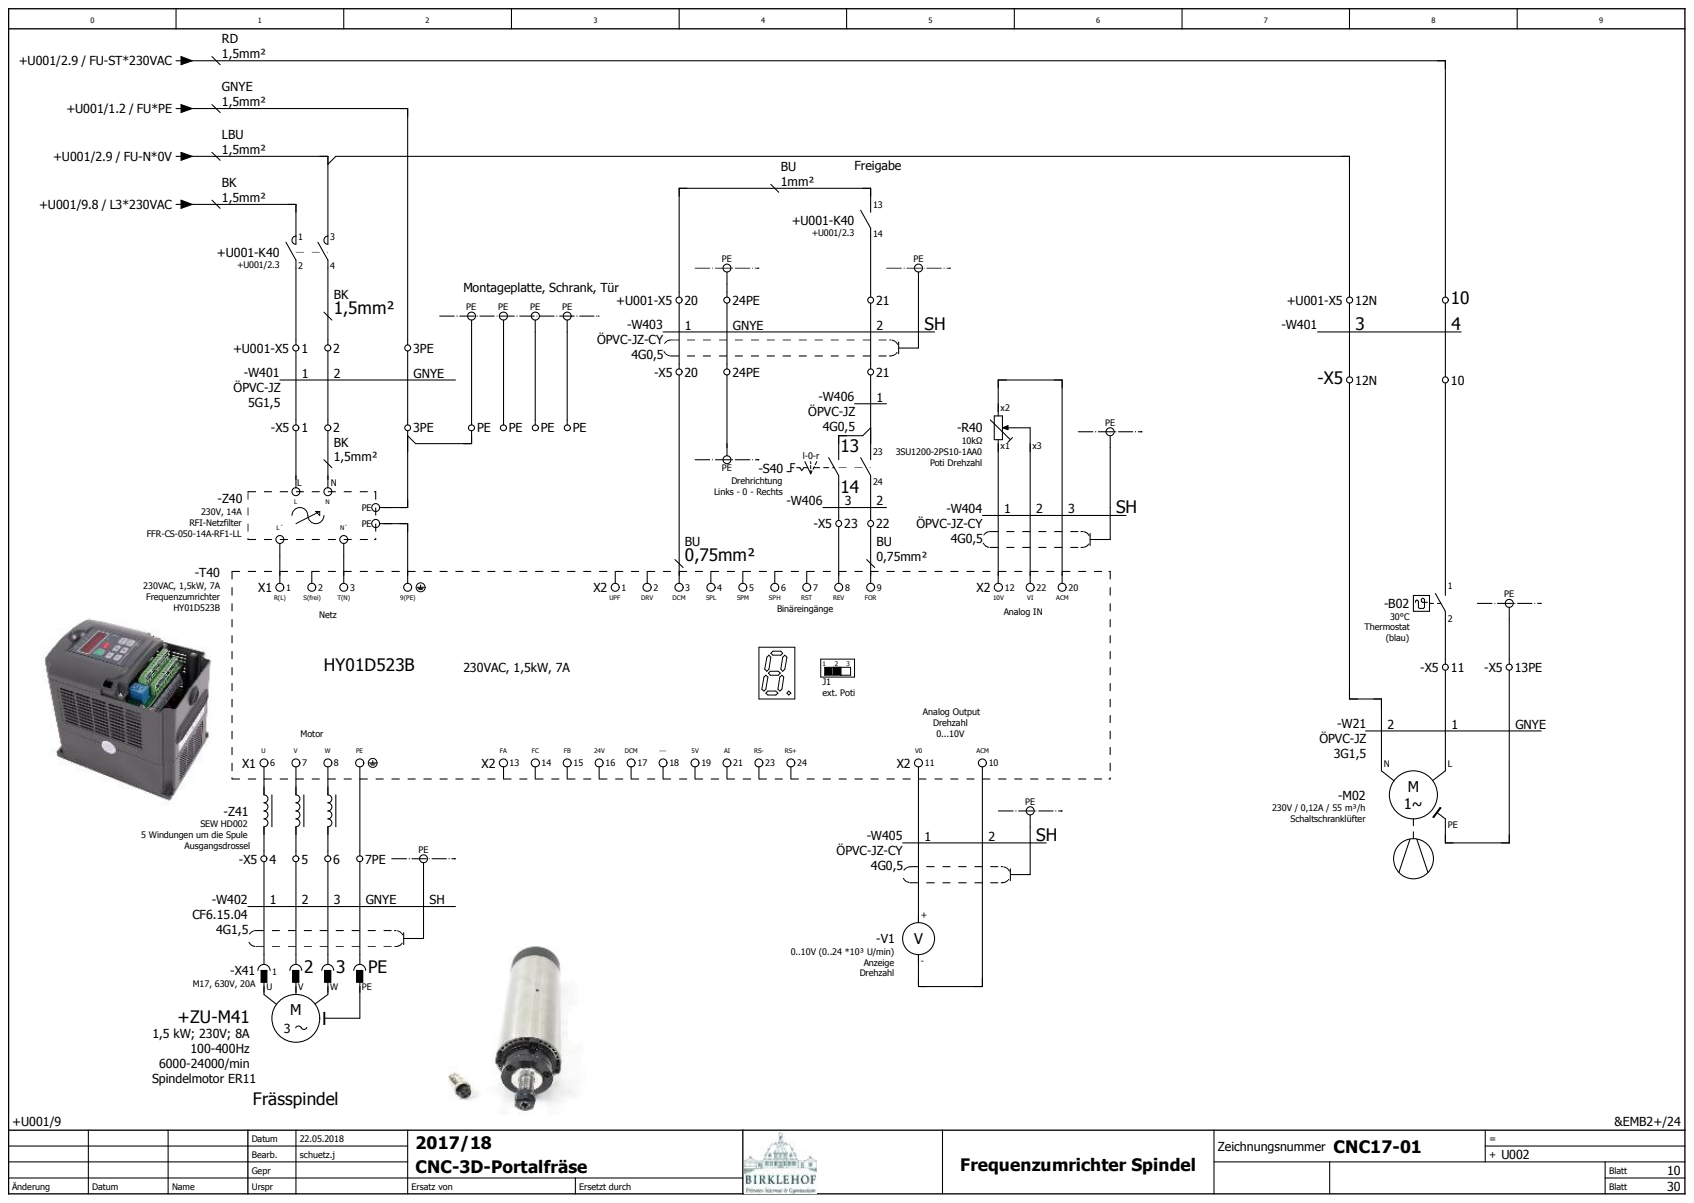
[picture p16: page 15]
U002 Frequenzumrichter Spindel; &EMB2+/24; Frässpindel; J1 ext. Poti; Freigabe; 1mm²; GNYE; +ZU-M41 1,5 kW; 230V; 8A 100-400Hz 6000-24000/min Spindelmotor ER11; -T40 230VAC, 1,5kW, 7A Frequenzumrichter HY01D523B; 230VAC, 1,5kW, 7A; UPF; Binäreingänge; DRV; DCM; SPL; SPM; SPH; RST; REV; FOR; Analog Output Drehzahl 0...10V; ACM 10; Motor; Netz; S(frei); -Z41 SEW HD002; Ausgangsdrossel; 1,5mm²; LBU; -B02 30°C Thermostat (blau); -M02 230V / 0,12A / 55 m³/h Schaltschranklüfter; -W21 ÖPVC-JZ 3G1,5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

Montageplatte, Schrank, Tür

FFR-CS-050-14A-RF1-LL

5 Windungen um die Spule

ÖPVC-JZ-CY

&EFS+U002/10

## Kabelübersicht : =-W0 -

=-W504

&EMA1/15

F10_001

Kabelname | | | Kabeltyp | alle Adern | verwendete Adern Ziel (bis) | Querschnitt [mm] | Länge [m] | Funktionstext | Grafikseite des Kabelplans Quelle (von)
-W0 | +U001-X0 | +U001-X00-CEE16A | NSSHÖU | 5G | 5 | 1,5mm² | 5
-W10 | +U001-X0 | +U002-S01 | ÖPVC-JZ | 3G | 2 | 1,5
-W11 | +U001-X0 | +U001-M01 | ÖPVC-JZ | 3G | 3 | 1,0
-W011 | +U001-X4 | +U001-U01 | ÖPVC-JZ | 4G | 2 | 0,5
-W21 | +U002-X5 | +U002-M02 | ÖPVC-JZ | 3G | 3 | 1,5
-W40 | | +U001-T01 | NYFAZ | 2x | 2 | 0,75
-W101 | +U001-X1 | +XV-M11 | YSLY-CY-JZ | 5G | 5 | 0,75
| | PE
-W102 | +U001-X1 | +XV-M12 | YSLY-CY-JZ | 5G | 5 | 0,75
| | PE
-W103 | +U001-U03 | +U001-U11 | LIYCY | 4x | 3 | 0,5
-W104 | +U001-U03 | +U001-U12 | LIYCY | 4x | 3 | 0,5
-W105 | +U001-X4 | +XV-S11 | ÖPVC-JZ | 3G | 2 | 0,75
-W106 | +U001-X4 | +XZ-S12 | | | 2
-W201 | +U001-X2 | +YR-M21 | CF6.10.05 | 5G | 5 | 1
| | PE
-W202 | +U001-U03 | +U001-U21 | LIYCY | 4x | 3 | 0,5
-W203 | +U001-X4 | +YR-S21 | CF6.07.03 | 3G | 2 | 0,75
-W204 | +U001-X4 | +YL-S22 | | | 2
-W301 | +U001-X3 | +ZO-M31 | CF6.10.05 | 5G | 5 | 1
| | PE
-W302 | +U001-U03 | +U001-U31 | LIYCY | 4x | 3 | 0,5
-W303 | +U001-X4 | +ZO-S31 | CF6.07.03 | 3G | 2 | 0,75
-W304 | +U001-X4 | +ZU-S32 | | | 2
-W401 | +U001-X5 | +U002-X5 | ÖPVC-JZ | 5G | 5 | 1,5
-W402 | +U002-X5 | +U002-X41 | CF6.15.04 | 4G | 5 | 1,5
| | PE
-W403 | +U001-X5 | +U002-X5 | ÖPVC-JZ-CY | 4G | 3 | 0,5
-W404 | +U002-R40 | +U002-T40 | ÖPVC-JZ-CY | 4G | 3 | 0,5
-W405 | +U002-T40 | +U002-V1 | ÖPVC-JZ-CY | 4G | 3 | 0,5
| | PE
-W406 | +U002-X5 | +U002-S40 | ÖPVC-JZ | 4G | 4 | 0,5
-W501 | +U001-X6 | +ZU-M51 | CF6.10.05 | 5G | 5 | 1
| | PE
-W502 | +U001-X6 | +ZU-E51 | CF6.15.04 | 4G | 3 | 1,5
| | PE
-W503 | +U001-X6 | +ZU-B51 | CF5.10.07 | 7G | 5 | 1
| | +ZU-M52
| | +U001-X6
-W504 | +U001-U03 | +U001-U51 | LIYCY | 4x | 3 | 0,5

# Kabelübersicht

| | | | | | | | Leiste +U001-X0

# Klemmenplan

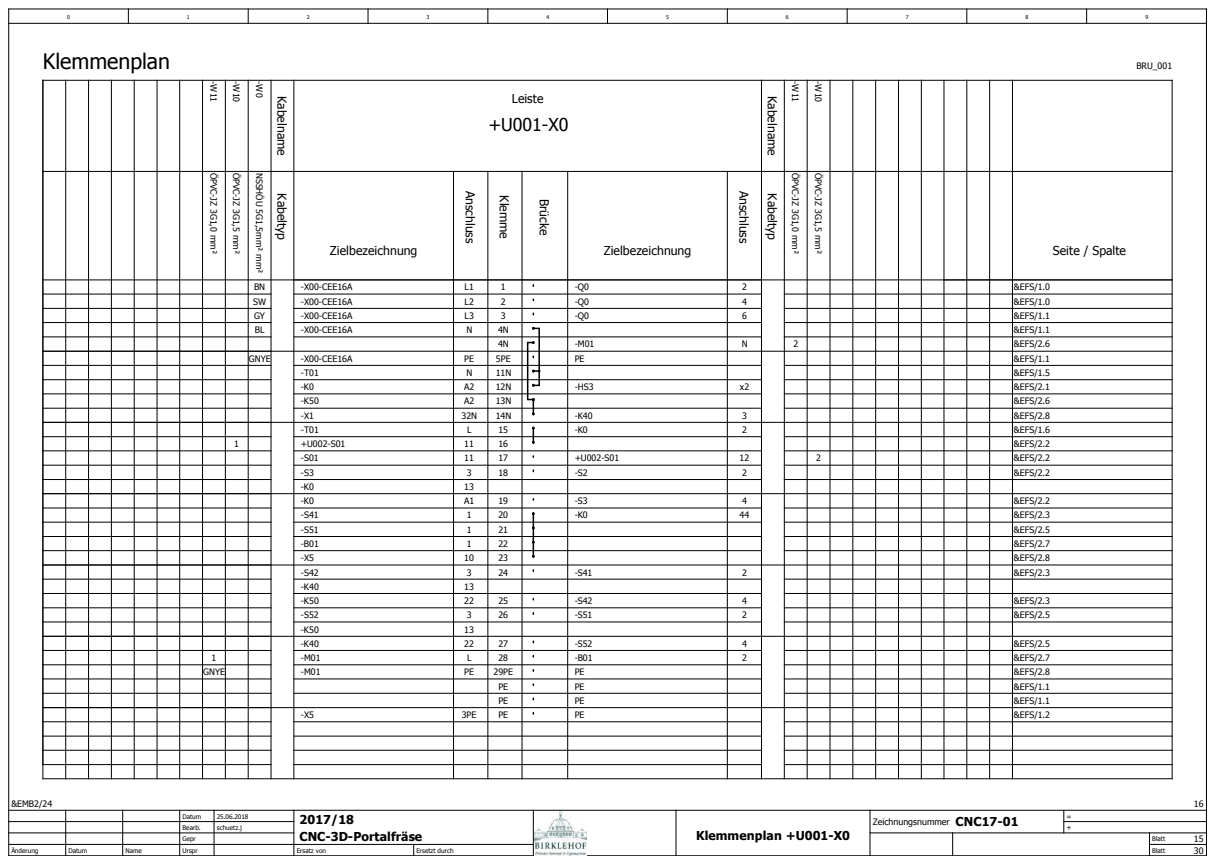
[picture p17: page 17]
&EMB2/24; Klemmenplan +U001-X0; Kabeltyp; Anschluss; Klemme; Brücke; Kabelname; BRU_001; -W0 NSSHÖU 5G1,5mm² mm²

-W11 ÖPVC-JZ 3G1,0 mm²

-W10 ÖPVC-JZ 3G1,5 mm²

ÖPVC-JZ 3G1,0 mm² -W11

ÖPVC-JZ 3G1,5 mm² -W10

Zielbezeichnung | | | Zielbezeichnung | | | | | | Seite / Spalte

BN | -X00-CEE16A | L1 | 1 | -Q0 | 2 | | | | | &EFS/1.0
SW | -X00-CEE16A | L2 | 2 | -Q0 | 4 | | | | | &EFS/1.0
GY | -X00-CEE16A | L3 | 3 | -Q0 | 6 | | | | | &EFS/1.1
BL | -X00-CEE16A | N | 4N | | | | | | | | &EFS/1.1

4N | | -M01 | N | | 2 | | | &EFS/2.6

GNYE | -X00-CEE16A | PE | 5PE | | PE | | | | | | &EFS/1.1

-T01 | N | 11N | | | | | | | | &EFS/1.5
-K0 | A2 | 12N | | -HS3 | x2 | | | | | &EFS/2.1
-K50 | A2 | 13N | | | | | | | | | | | | &EFS/2.6
-X1 | 32N | 14N | -K40 | 3 | | | | | | | | | | &EFS/2.8
-T01 | L | 15 | | -K0 | 2 | | | | | &EFS/1.6

1 | | +U002-S01 | 11 | 16 | | | | | | | | &EFS/2.2

-S01 | 11 | 17 | | +U002-S01 | 12 | | | 2 | | &EFS/2.2
-S3 | 3 | 18 | | -S2 | 2 | | | | | &EFS/2.2
-K0 | 13
-K0 | A1 | 19 | | -S3 | 4 | | | | | &EFS/2.2
-S41 | 1 | 20 | | -K0 | 44 | | | | | &EFS/2.3
-S51 | 1 | 21 | | | | | | | | &EFS/2.5
-B01 | 1 | 22 | | | | | | | | &EFS/2.7
-X5 | 10 | 23 | | | | | | | | &EFS/2.8
-S42 | 3 | 24 | | -S41 | 2 | | | | | &EFS/2.3
-K40 | 13
-K50 | 22 | 25 | | -S42 | 4 | | | | | &EFS/2.3
-S52 | 3 | 26 | | -S51 | 2 | | | | | &EFS/2.5
-K50 | 13
-K40 | 22 | 27 | | -S52 | 4 | | | | | &EFS/2.5

1 | | | -M01 | L | 28 | | -B01 | 2 | | | | | &EFS/2.7
GNYE | | | -M01 | PE | 29PE | | PE | | | | | | &EFS/2.8

PE | | PE | | | | | | &EFS/1.1

-X5 | 3PE | PE | | PE | | | | | | &EFS/1.2

## Klemmenplan +U001-X1

## Kabeltyp

## Anschluss

## Klemme

## Brücke

## Kabelname

| | Leiste +U001-X1
| | Zielbezeichnung | | | Zielbezeichnung | | | Seite / Spalte
| | -T11 | L | 30 | | -K0 | 43 | | &EFS/6.2
| | -T12 | L | 31 | | | | | &EFS/6.5
| | -X0 | 14N | 32N | | -T11 | N | | &EFS/6.1
| | -X2 | 32N | 33N | | -T12 | N | | &EFS/6.4
| | -T11 | 0V | 34PE | | PE | | | &EFS/6.2
| | -T11 | PE
| 1 | +XV-M11 | RD | 35 | | -U11 | A+ | | &EFS/6.2
| | -T12 | 0V | 35PE | | PE | | | &EFS/6.6
| | -T12 | PE
| 2 | +XV-M11 | GN | 36 | | -U11 | A- | | &EFS/6.2
| 3 | +XV-M11 | YE | 37 | | -U11 | B+ | | &EFS/6.2
| 4 | +XV-M11 | BU | 39 | | -U11 | B- | | &EFS/6.2
1 | | +XV-M12 | RD | 39 | | -U12 | A+ | | &EFS/6.5
2 | | +XV-M12 | GN | 40 | | -U12 | A- | | &EFS/6.5
3 | | +XV-M12 | YE | 41 | | -U12 | B+ | | &EFS/6.5
4 | | +XV-M12 | BU | 42 | | -U12 | B- | | &EFS/6.5

BRU_001

## Kabelname

# Klemmenplan

## Anschluss

## Kabeltyp

-W101 YSLY-CY-JZ 5G0,75 mm²

-W102 YSLY-CY-JZ 5G0,75 mm²

## Klemmenplan +U001-X2

## Kabeltyp

## Anschluss

## Klemme

## Brücke

## Kabelname

| Leiste +U001-X2
| Zielbezeichnung | | | Zielbezeichnung | | Seite / Spalte
| -T21 | L | 30 | -K0 | 3 | &EFS/7.2
| | | | -X3 | 30
| -X1 | 33N | 32N | -T21 | N | &EFS/7.1
| -X3 | 32N
| -T21 | 0V | 34PE | PE | | &EFS/7.2
| -T21 | PE
1 | +YR-M21 | RD | 36 | -U21 | A+ | &EFS/7.2
2 | +YR-M21 | GN | 37 | -U21 | A- | &EFS/7.2
3 | +YR-M21 | YE | 38 | -U21 | B+ | &EFS/7.2
4 | +YR-M21 | BU | 39 | -U21 | B- | &EFS/7.2

BRU_001

## Kabelname

# Klemmenplan

## Anschluss

## Kabeltyp

-W201 CF6.10.05 5G1 mm²

## Klemmenplan +U001-X3

## Kabeltyp

## Anschluss

## Klemme

## Brücke

## Kabelname

| Leiste +U001-X3
| Zielbezeichnung | | | Zielbezeichnung | | Seite / Spalte
| -T31 | L | 30 | -X2 | 30 | &EFS/8.2
| -X2 | 32N | 32N | -T31 | N | &EFS/8.1
| -X6 | 31N
| -T31 | 0V | 34PE | PE | | &EFS/8.2
| -T31 | PE
1 | +ZO-M31 | RD | 36 | -U31 | A+ | &EFS/8.2
2 | +ZO-M31 | GN | 37 | -U31 | A- | &EFS/8.2
3 | +ZO-M31 | YE | 38 | -U31 | B+ | &EFS/8.2
4 | +ZO-M31 | BU | 39 | -U31 | B- | &EFS/8.2

BRU_001

## Kabelname

# Klemmenplan

## Anschluss

## Kabeltyp

-W301 CF6.10.05 5G1 mm²

| | | | | | | | | | Leiste +U001-X4

# Klemmenplan

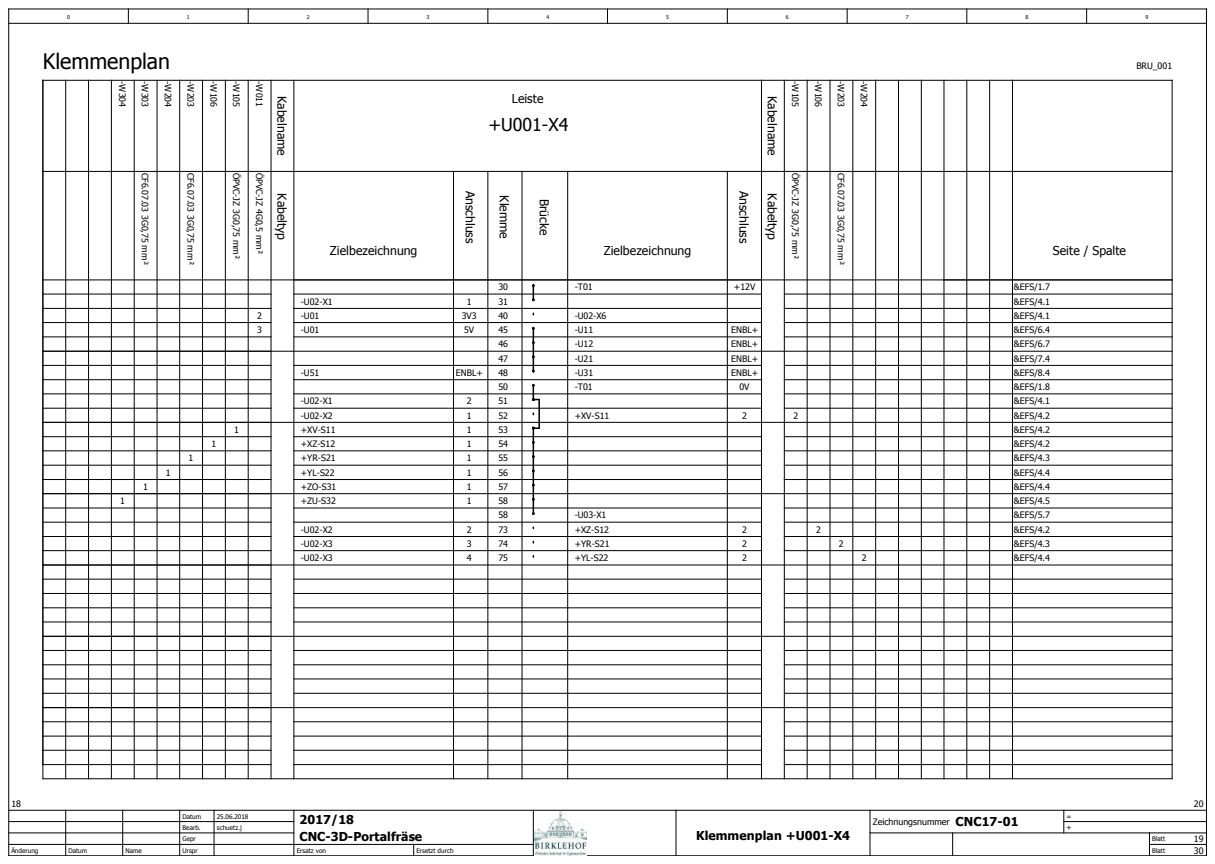
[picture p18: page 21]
Klemmenplan +U001-X4; Kabeltyp; Anschluss; Klemme; Brücke; Kabelname; BRU_001; CF6.07.03 3G0,75 mm² -W203; CF6.07.03 3G0,75 mm²

-W011 ÖPVC-JZ 4G0,5 mm²

ÖPVC-JZ 3G0,75 mm² -W105

ÖPVC-JZ 3G0,75 mm²

Zielbezeichnung | | | Zielbezeichnung | | | | | | | Seite / Spalte

30 | | -T01 | +12V | | | | | | &EFS/1.7

-U02-X1 | 1 | 31 | | | | | | | | | &EFS/4.1

2 | -U01 | 3V3 | 40 | | -U02-X6 | | | | | | | &EFS/4.1
3 | -U01 | 5V | 45 | | -U11 | ENBL+ | | | | | | &EFS/6.4

46 | | -U12 | ENBL+ | | | | | | &EFS/6.7
47 | | -U21 | ENBL+ | | | | | | &EFS/7.4

-U51 | ENBL+ | 48 | | -U31 | ENBL+ | | | | | | &EFS/8.4

50 | | -T01 | 0V | | | | | | &EFS/1.8

-U02-X1 | 2 | 51 | | | | | | | | | | | | | | &EFS/4.1
-U02-X2 | 1 | 52 | | | +XV-S11 | 2 | | 2 | | | | | | | | &EFS/4.2

1 | | +XV-S11 | 1 | 53 | | | | | | | | | &EFS/4.2
1 | | | +XZ-S12 | 1 | 54 | | | | | | | | | &EFS/4.2
1 | | | | +YR-S21 | 1 | 55 | | | | | | | | | &EFS/4.3
1 | | | | | +YL-S22 | 1 | 56 | | | | | | | | | &EFS/4.4
1 | | | | | | +ZO-S31 | 1 | 57 | | | | | | | | | &EFS/4.4
1 | | | | | | | +ZU-S32 | 1 | 58 | | | | | | | | | &EFS/4.5

58 | | -U03-X1 | | | | | | | &EFS/5.7

-U02-X2 | 2 | 73 | | +XZ-S12 | 2 | | 2 | | | | &EFS/4.2
-U02-X3 | 3 | 74 | | +YR-S21 | 2 | | | 2 | | | &EFS/4.3
-U02-X3 | 4 | 75 | | +YL-S22 | 2 | | | | 2 | | &EFS/4.4

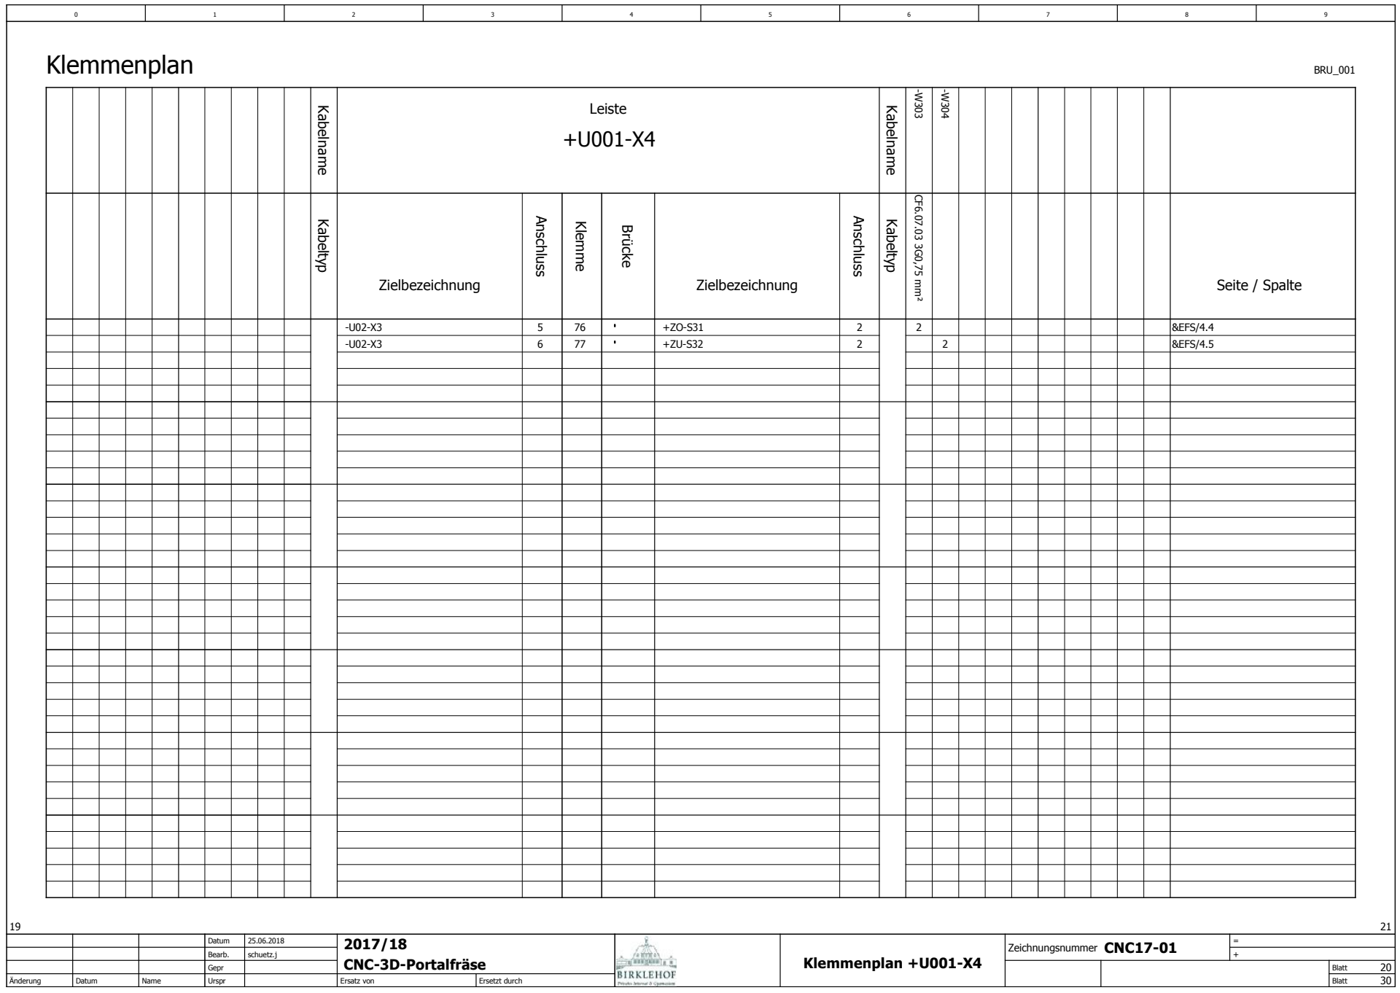
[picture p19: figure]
Klemmenplan +U001-X4; Kabeltyp; Anschluss; Klemme; Brücke; Kabelname; Leiste +U001-X4; BRU_001; Klemmenplan; CF6.07.03 3G0,75 mm² -W303; &EFS/4.4; &EFS/4.5

Zielbezeichnung | | | Zielbezeichnung | | | | Seite / Spalte

## Klemmenplan +U001-X5

## Kabeltyp

## Anschluss

## Klemme

## Brücke

## Kabelname

| | | | | Leiste +U001-X5
| | | | | Zielbezeichnung | | | Zielbezeichnung | | | Seite / Spalte
| | | | 1 | +U002-X5 | 1 | 1 | -K40 | 2 | | &EFS+U002/10.1
| | | | 2 | +U002-X5 | 2 | 2 | -K40 | 4 | | &EFS+U002/10.1
3PE | -X0 | PE | | | | | | | | &EFS/1.2
| | | | GNYE | +U002-X5 | 3PE | 3PE | | | | &EFS+U002/10.2
| | | | 4 | +U002-X5 | 10 | 10 | -X0 | 23 | | &EFS+U002/10.8
| | | | 3 | +U002-X5 | 12N | 12N | -K40 | 3 | | &EFS+U002/10.8
| | | 1 | | +U002-X5 | 20 | 20 | -K40 | 13 | | &EFS+U002/10.4
| | | 2 | | +U002-X5 | 21 | 21 | -K40 | 14 | | &EFS+U002/10.5
| | | GNYE | | +U002-X5 | 24PE | 24PE | PE | | | &EFS+U002/10.4

BRU_001

## Kabelname

# Klemmenplan

## Anschluss

## Kabeltyp

-W401 ÖPVC-JZ 5G1,5 mm²

-W403 ÖPVC-JZ-CY 4G0,5 mm²

## Klemmenplan +U001-X6

## Kabeltyp

## Anschluss

## Klemme

## Brücke

## Kabelname

| | | | | | | | Leiste +U001-X6
| | | | | | | | Zielbezeichnung | | | Zielbezeichnung | | | Seite / Spalte
| | | | | | | | -T51 | L | 30 | -K50 | 2 | | &EFS/9.3
| | | | | | | | -X3 | 32N | 31N | -T51 | N | | &EFS/9.1
| | | | | | | | -T51 | 0V | 32PE | PE | | | &EFS/9.3
| | | | | | | | -T51 | PE
| | | | | | | 1 | +ZU-M51 | BK | 33 | -U51 | A+ | | &EFS/9.2
| | | | | | | 2 | +ZU-M51 | RT | 34 | -U51 | A- | | &EFS/9.2
| | | | | | | 3 | +ZU-M51 | GN | 35 | -U51 | B+ | | &EFS/9.2
| | | | | | | 4 | +ZU-M51 | BU | 36 | -U51 | B- | | &EFS/9.3
-U51 | VDC | 40 | -T51 | +12V | | | | | | | | | &EFS/9.2
-K50 | 5 | 41 | | | | | | | | | | | &EFS/9.5
| | | | | | | | | | 42 | | | | &EFS/9.6
-U51 | GND | 43 | -T51 | 0V | | | | | | | | | &EFS/9.3
| | 44 | | | | | | | | | | | &EFS/9.5
| | 45 | | | | | | | | | | | &EFS/9.6
+ZU-E51 | RD | 46 | -K50 | 6 | | | | | | | | | &EFS/9.5
| | | | | | 2 | | +ZU-E51 | YE | 47 | | | | &EFS/9.5
| | | | | | | | +ZU-B51 | + | 51 | | | | &EFS/9.6
| | | | | 2 | | | +ZU-B51 | BK | 52 | | | | &EFS/9.7
| | | | | 3 | | | +ZU-M52 | rd+ | 53 | | | | &EFS/9.7
| | | | | 4 | | | +ZU-M52 | bk- | 54 | | | | &EFS/9.8
| | | | | 5 | | | -X6 | ye Tacho | 55 | | | | &EFS/9.8

BRU_001

## Kabelname

# Klemmenplan

## Anschluss

## Kabeltyp

-W501 CF6.10.05 5G1 mm²

-W502 CF6.15.04 4G1,5 mm² 1

-W503 CF5.10.07 7G1 mm² 1

## Klemmenplan +U002-X5

&EPC/25

## Kabeltyp

## Anschluss

## Klemme

## Brücke

## Kabelname

| | | Leiste +U002-X5
| | | Zielbezeichnung | | | Zielbezeichnung | | | | | Seite / Spalte
| | | -Z40 | X1 | 1 | +U001-X5 | 1 | 1 | | | &EFS/10.1
| | | -Z40 | X1 | 2 | +U001-X5 | 2 | 2 | | | &EFS/10.1
| | | -Z40 | PE | 3PE | +U001-X5 | 3PE | GNYE | | | &EFS/10.2
| | 1 | -X41 | 1 | 4 | -Z41 | | | | | &EFS/10.1
| | 2 | -X41 | 2 | 5 | -Z41 | | | | | &EFS/10.1
| | 3 | -X41 | 3 | 6 | -Z41 | | | | | &EFS/10.1
| | GNYE | -X41 | PE | 7PE | -T40 | X1:X1.9 | | | | &EFS/10.2
| | | -B02 | 1 | 10 | +U001-X5 | 10 | 4 | | | &EFS/10.8
| 1 | | -M02 | L | 11 | -B02 | 2 | | | | &EFS/10.8
| 2 | | -M02 | N | 12N | +U001-X5 | 12N | 3 | | | &EFS/10.8
| GNYE | | -M02 | PE | 13PE | PE | | | | | &EFS/10.8
| | | -T40 | X2:X2.3 | 20 | +U001-X5 | 20 | | 1 | | &EFS/10.4
1 | | | -S40 | 23 | 21 | +U001-X5 | 21 | | 2 | | &EFS/10.5
1 | | | -S40 | 13
| | | -T40 | X2:X2.9 | 22 | -S40 | 24 | | | 2 | &EFS/10.5
| | | -T40 | X2:X2.8 | 23 | -S40 | 14 | | | 3 | &EFS/10.4
| | | PE | | 24PE | +U001-X5 | 24PE | | GNYE | | &EFS/10.4
| | | | | PE | PE | | | | | &EFS/10.2
| | | | | PE | PE | | | | | &EFS/10.2
| | | | | PE | PE | | | | | &EFS/10.3
| | | | | PE | PE | | | | | &EFS/10.3

BRU_001

## Kabelname

# Klemmenplan

## Anschluss

## Kabeltyp

ÖPVC-JZ 5G1,5 mm²

-W402

-W401

CF6.15.04 4G1,5 mm²

-W21 ÖPVC-JZ 3G1,5 mm²

ÖPVC-JZ-CY 4G0,5 mm² -W403

-W406 ÖPVC-JZ 4G0,5 mm²

ÖPVC-JZ 4G0,5 mm² -W406

&EMA1/23

## Artikelstückliste : - MEN.Pro Top13A

Betriebsmittelkennzeichen | Menge | Bezeichnung | Typnummer | Lieferant | Artikelnummer
| 0
+U001-B01 | 1 | | | | 8MR2170-1BB
+U001-F0 | 1 | Motorschutzschalter S0, 11-16A, 1S + 1Ö, Class10, Schraubanschluss | 3RV2021-4AA15 | SIE | SIE.3RV2021-4AA15
+U001-HS3 | 0
+U001-HS42 | 0
+U001-HS52 | 0
+U001-K0 | 1 | | | | SIE.3RT2017-1AP04
+U001-K40 | 1 | SCHUETZ, AC-3, 3KW/400V, 2S+2OE, AC 230V, 50/60 HZ | 3RT2015-1AP04-3MA0 | SIE | SIE.3RT2015-1AP04-3MA0
+U001-K50 | 1 | SCHUETZ, AC-3, 3KW/400V, 2S+2OE, AC 230V, 50/60 HZ | 3RT2015-1AP04-3MA0 | SIE | SIE.3RT2015-1AP04-3MA0
+U001-M01 | 1 | | | | SK 3238.100
+U001-M01 | 1 | | | | SK 3238.200
+U001-M01 | 1 | | | | Caleg.Uniflex-RE 600/400/250
+U001-M01 | 4 | | | | SZ2508.010
+U001-Q0 | 1 | NOT-AUS-SCH 16A/690V 400V/7,5KW | 3LD2003-0TK53 | SIE | SIE.3LD2003-0TK53
+U001-Q0 | 1 | | | | SIE.3LD9286-1A
+U001-Q0 | 2 | | | | SIE.3LD9201-1A
+U001-S01 | 1 | | | | SIE.3SB2203-1AC01
+U001-S2 | 1 | | | | SIE.3SU1100-0AB20-1CA0
+U001-S3 | 1 | | | | SIE.3SU1100-0AB40-1BA0
+U001-S41 | 1 | | | | SIE.3SU1100-0AB20-1CA0
+U001-S42 | 1 | | | | SIE.3SU1100-0AB40-1BA0
+U001-S51 | 1 | | | | SIE.3SU1100-0AB20-1CA0
+U001-S52 | 1 | | | | SIE.3SU1100-0AB40-1BA0
+U001-T01 | 1 | | | | Wago.787-1001
+U001-T11 | 1 | | | | Longs.S350-60
+U001-T12 | 1 | | | | Longs.S350-60
+U001-T21 | 1 | | | | Longs.S350-60
+U001-T31 | 1 | | | | Longs.S350-60
+U001-T51 | 1 | | | | Longs.S100-12
+U001-U01 | 1 | | | | Arduino Due
+U001-U02 | 1 | | | | Arduino Due
+U001-U02-V1 | 0
+U001-U02-V2 | 0
+U001-U02-V3 | 0
+U001-U02-V4 | 0
+U001-U02-V5 | 0
+U001-U02-V6 | 0
+U001-U03 | 1 | | | | Arduino Due
+U001-U03-V1 | 0
+U001-U03-V2 | 0
+U001-U03-V3 | 0
+U001-U03-V4 | 0
+U001-U03-V5 | 0
+U001-U03-V6 | 0
+U001-U03-V7 | 0
+U001-U03-V8 | 0
+U001-U03-V9 | 0
+U001-U03-V10 | 0
+U001-U03-V11 | 0
+U001-U03-V12 | 0
+U001-U11 | 1 | | | | Longs. DM860A
+U001-U12 | 1 | | | | Longs. DM860A
+U001-U21 | 1 | | | | Longs. DM860A
+U001-U31 | 1 | | | | Longs. DM860A
+U001-U51 | 1 | | | | Longs. DM860A
+U001-X00 | 1 | | | | MEN.Pro Top13A
Artikelstückliste | F01_001

## Artikelstückliste : Pollin.250411 -Eaton.LS-11/L_#266110

&ETL/30

Betriebsmittelkennzeichen | Menge | Bezeichnung | Typnummer | Lieferant | Artikelnummer
+U001-Z11 | 1 | | | | Pollin.250411
+U001-Z12 | 1 | | | | Pollin.250411
+U001-Z21 | 1 | | | | Pollin.250411
+U001-Z31 | 1 | | | | Pollin.250411
+U001-Z51 | 1 | | | | Pollin.250411
+U002-B02 | 1 | | | | 8MR2170-1BB
+U002-M02 | 1 | | | | SK 3238.100
+U002-M02 | 1 | | | | SK 3238.200
+U002-M02 | 1 | | | | Caleg.Uniflex-RE 380/380/210
+U002-M02 | 4 | | | | SZ2508.010
+U002-R40 | 1 | | | | SIE.3SU1200-2PS10-1AA0
+U002-S01 | 1 | | | | SCHN.XALK178E
+U002-S40 | 1 | | | | SIE.3SU1100-2BL60-1NA0
+U002-T40 | 1 | | | | Huanyang.HY01D523B
+U002-V1 | 0
+U002-Z40 | 1 | | | | Rasmi Electronics.FFR-CS-050-14A-RF1LL
+U002-Z41 | 1 | | | | SEW.HD002
+U002-Z41 | 0
+XV-M11 | 1 | | | | Longs.34HS1456
+XV-M12 | 1 | | | | Longs.34HS1456
+XV-S11 | 1 | | | | Eaton.LS-11/L_#266110
+XZ-S12 | 1 | | | | Eaton.LS-11/L_#266110
+YR-M21 | 1 | | | | Longs.34HS1456
+YR-S21 | 1 | | | | Eaton.LS-11/L_#266110
+YL-S22 | 1 | | | | Eaton.LS-11/L_#266110
+ZO-M31 | 1 | | | | Longs.34HS1456
+ZO-S31 | 1 | | | | Eaton.LS-11/L_#266110
+ZU-B51 | 0
+ZU-E51 | 0
+ZU-M41 | 0
+ZU-M51 | 1 | | | | Longs.34HS1456
+ZU-M52 | 0
+ZU-S32 | 1 | | | | Eaton.LS-11/L_#266110
Artikelstückliste | F01_001

&EPC/26

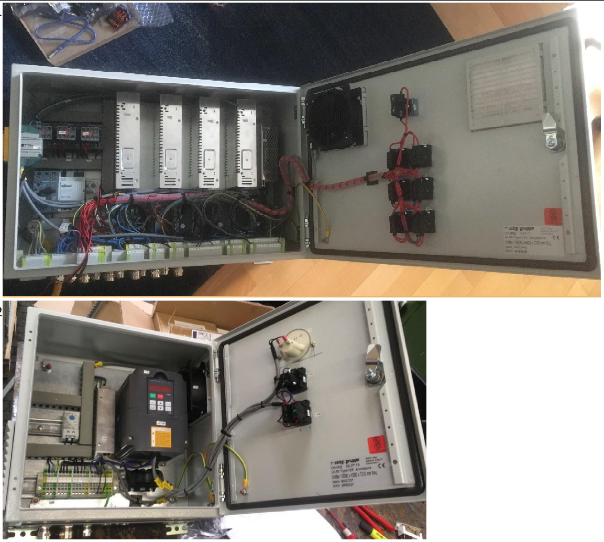
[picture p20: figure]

28.05.2018 | Schaltschrankaufbau
schuetz | | +

+U001

+U002

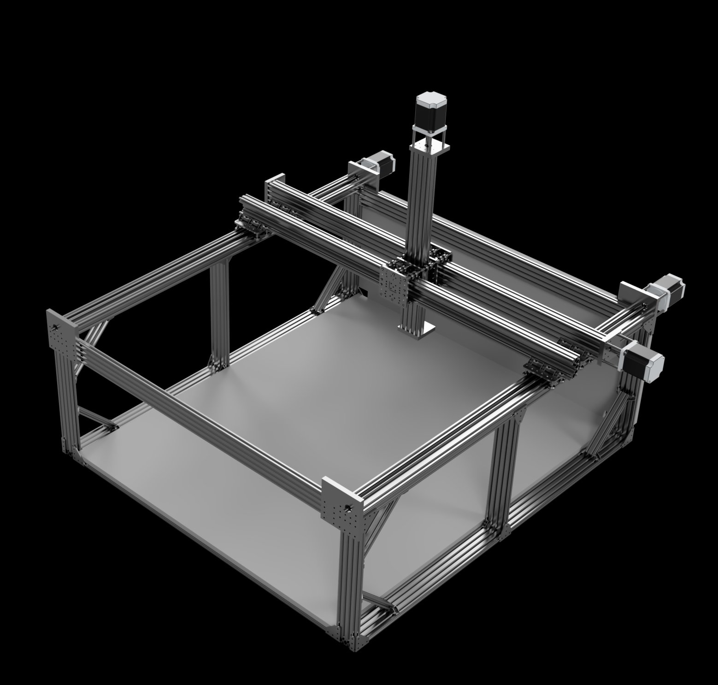
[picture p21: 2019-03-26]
CNC-Mill-v3_Render.jpg

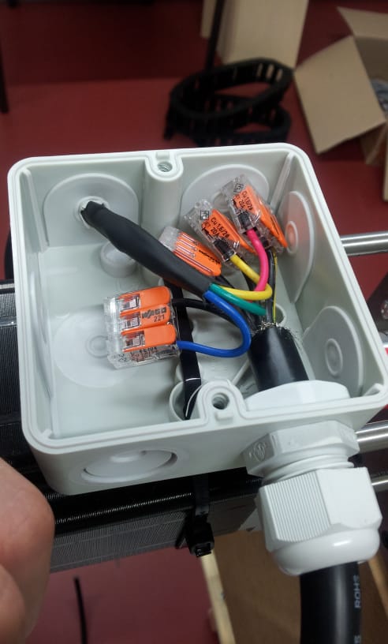
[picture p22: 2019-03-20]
Bilder/Verkabelung in Kabelboxen.jpeg

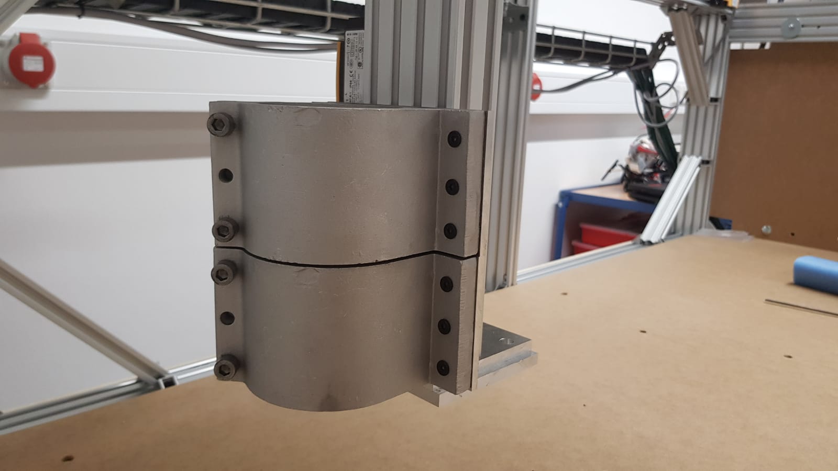
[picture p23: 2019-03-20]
Bilder/Halter Spindel.jpeg

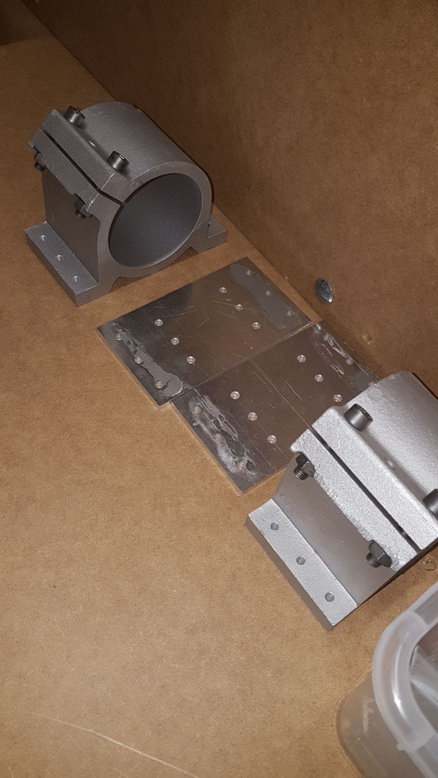
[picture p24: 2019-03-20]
Bilder/Halter Spindel einzelteile.jpeg

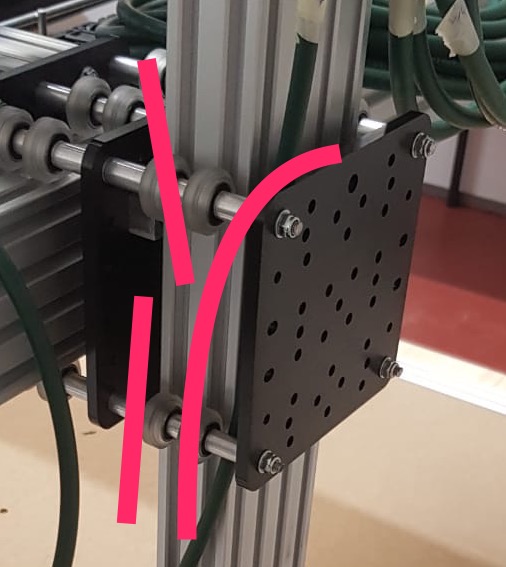
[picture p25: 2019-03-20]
Bilder/Verbiegung Z-Achse.jpeg

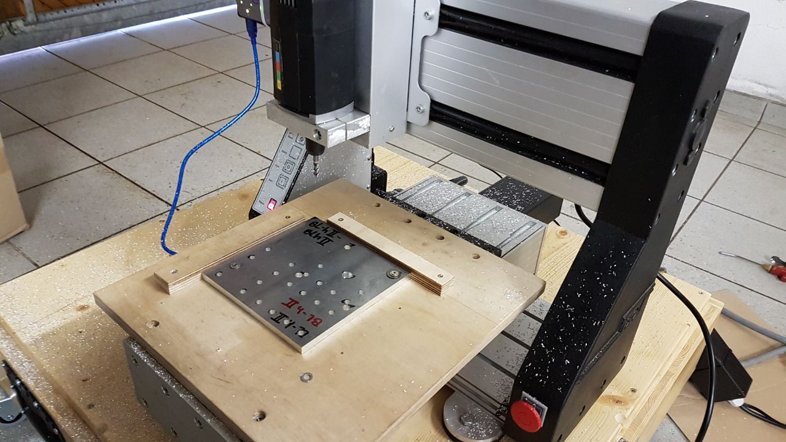
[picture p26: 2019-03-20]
Bilder/Fräsen 1.jpeg

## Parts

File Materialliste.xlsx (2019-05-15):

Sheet: Tabelle2
Kostenvoranschlag - MINT CNC-Fräse
Openbuilds | www.openbuildspartstore.com
Stückzahl | Name | Größe | Preis/Stück | Gesamt | Link | Kommentar
7 | V-Slot® Linear Rail | 2cm x 8 cm x 150 cm | 25.11 € | 175.77 € | http://openbuildspartstore.com/v-slot-linear-rail/ | 5 davon müssen auf 125 cm gekürzt werden - alles in silber
6 | V-Slot® Linear Rail | 2cm x 8 cm x 50 cm | 8.37 € | 50.22 € | http://openbuildspartstore.com/v-slot-linear-rail/ | silber
4 | V-Slot® Linear Rail | 2 cm x 4 cm x 50 cm | 5.44 € | 21.76 € | http://openbuildspartstore.com/v-slot-linear-rail/ | silber - die müssen wir in der Schreinerei halbieren - ist billiger als 25cm
4 | C-Beam® Linear Rail | 4cm x 8 cm x 150 cm | 32.65 € | 130.60 € | http://openbuildspartstore.com/c-beam-linear-rail/ | silber - hier gibt es keine auswahl
1 | C-Beam® Linear Rail | 4cm x 8 cm x 100 cm | 23.44 € | 23.44 € | http://openbuildspartstore.com/c-beam-linear-rail/ | silber - hier gibt es keine auswahl
78 | Cast Corner Bracket | 2 cm x 2 cm x 1,7 cm | 1.26 € | 98.28 € | http://openbuildspartstore.com/cast-corner-bracket/
12 | 90 Degree Joining Plate | 6 cm x 6 cm x 0,4 cm | 4.02 € | 48.24 € | http://openbuildspartstore.com/90-degree-joining-plate/
4 | T Joining Plate | 6 cm x 6 cm x 0,4 cm | 3.89 € | 15.56 € | http://openbuildspartstore.com/t-joining-plate/
4 | 3 Hole Joining Strip Plate | 6 cm x 1,8 cm x 0,4 cm | 1.72 € | 6.88 € | http://openbuildspartstore.com/3-hole-joining-strip-plate/
6 | Low Profile Screws M5 | M5 - 8 mm | 2.51 | 15.06 | http://openbuildspartstore.com/low-profile-screws-m5/ | 25er Pack: Benötigt: 124 Schrauben => 5 Packungen
3 | Low Profile Screws M5 | M5 - 10 mm | 2.68 | 8.04 | http://openbuildspartstore.com/low-profile-screws-m5/ | 25er Pack: Benötigt: 64 Schrauben => 3 Packungen
1 | Low Profile Screws M5 | M5 - 15 mm | 2.76 | 2.76 | http://openbuildspartstore.com/low-profile-screws-m5/ | 25er Pack: Benötigt: 12 Schrauben => 1 Packung
4 | Low Profile Screws M5 | M5 - 20mm | 2.85 | 11.4 | http://openbuildspartstore.com/low-profile-screws-m5/ | 25er Pack: Benötigt: 94 Schrauben => 4 Packungen
3 | Low Profile Screws M5 | M5 - 25 mm | 3.14 | 9.42 | http://openbuildspartstore.com/low-profile-screws-m5/ | 25er Pack: Benötigt: 56 Schrauben => 3 Packungen
1 | Low Profile Screws M5 | M5 - 45 mm | 3.98 | 3.98 | http://openbuildspartstore.com/low-profile-screws-m5/ | 25er Pack: Benötigt: 12 Schrauben => Packung
15 | Tee Nuts (25 Pack) | M5 | 4.14 | 62.1 | http://openbuildspartstore.com/tee-nuts-25-pack/ | 25er Pack: Benötigt: 350 Tee Nuts => 14 Packungen
10 | Aluminum Spacers | 9mm | 0.21 € | 2.10 € | http://openbuildspartstore.com/aluminum-spacers/
52 | Aluminum Spacers | 20mm | 0.29 € | 15.08 € | http://openbuildspartstore.com/aluminum-spacers/
32 | Precision Shim - 10x5x1mm | 10x5x1mm | 0.21 € | 6.72 € | http://openbuildspartstore.com/precision-shim-10x5x1mm/
56 | Xtreme Solid V Wheel™ Kit |  | 5.65 € | 316.40 € | http://openbuildspartstore.com/xtreme-solid-v-wheel-kit/
8 | C-Beam® Gantry Plate - XLarge |  | 12.51 € | 100.08 € | http://openbuildspartstore.com/c-beam-gantry-plate-xlarge/
 |  |  |  | 1123.89 € | zzgl. Versand
Schreinerei
Stückzahl | Name | Größe | Preis/Stück | Gesamt | Link | Kommentar
1 | MDF Platte | 150 cm x 125 cm x 1,9 cm |  | 0.00 € | Schreinerei
1 | MDF Platte | 141 cm x 54 cm x 1,9 cm |  | 0.00 € | Schreinerei
 |  |  |  |  | Preis abhängig
ebay - batho2010 | ebay.de
Stückzahl | Name | Größe | Preis/Stück | Gesamt | Link | Kommentar
8 | Aluminium Blech hochfest (7075) 8 mm Stark Zuschnitt frei wählbar | 15 cm x 15 cm x 0,8 cm | 6.00 € | 48.00 € | http://www.ebay.de/itm/Aluminium-Blech-hochfest-7075-8-mm-Stark-Zuschnitt-frei-wahlbar-/111645652297?var= | Ist AlZnMgCu1,5 => hart, aber gut zu fräsen
8 | Aluminium Blech hochfest (7075) 8 mm Stark Zuschnitt frei wählbar | 10 cm x 10 cm x 0,8 cm | 2.67 € | 21.36 € | http://www.ebay.de/itm/Aluminium-Blech-hochfest-7075-8-mm-Stark-Zuschnitt-frei-wahlbar-/111645652297?var= | Eigentlich nur 9,5cm, aber wenn es ein bisschen größer ist, ist egal
1 | Aluminium Plangefräst Alplan,Aluplan plangefräste Alu Platte alle Stärken wählba | 10 cm x 20 cm x 1,5 cm | 9.49 | 9.49 | http://www.ebay.de/itm/Aluminium-Plangefrast-Alplan-Aluplan-plangefraste-Alu-Platte-alle-Starken-wahlba-/121254993166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 | Daraus bekomme ich alle vier Mutterhalter. Die haben 80 mm x 33 mm
 | Versand |  |  | 5.00 €
 |  |  |  | 83.85 €
ebay - smalltec | ebay.de
Stückzahl | Name | Größe | Preis/Stück | Gesamt | Link | Kommentar
3 | Trapezgewindespindel TR 12x3 Rechts | 1601mm - 1700mm | 13.34 € | 40.02 € | http://www.ebay.de/itm/Trapezgewindespindel-TR-12x3-Rechts-/192252502309?var= | Können doch schon mit 1,6 m gekauft werden
1 | Trapezgewindespindel TR 12x3 Rechts | 801mm - 900mm | 9.09 € | 9.09 € | http://www.ebay.de/itm/Trapezgewindespindel-TR-12x3-Rechts-/192252502309?var= | Und auch kürzer
 | Versand |  |  | 6.70 €
 |  |  |  | 55.81 €
ebay - ebayplus | ebay.de
Stückzahl | Name | Größe | Preis/Stück | Gesamt | Link | Kommentar
1 | Stop-Muttern Selbstsichernde | M4 | 2.85 € | 2.85 € | http://www.ebay.de/itm/Stop-Muttern-Selbstsichernde-Stop-Muttern-Sicherungsmuttern-verzinkt-M3-M24-/282217367655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 | 20er Pack: Benötigt werden 16 => 1 Packung
2 | Stop-Muttern Selbstsichernde | M5 | 2.80 € | 5.60 € | http://www.ebay.de/itm/Stop-Muttern-Selbstsichernde-Stop-Muttern-Sicherungsmuttern-verzinkt-M3-M24-/282217367655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 | 20er Pack: Benötigt werden 28 => 2 Packungen
1 | Stop-Muttern Selbstsichernde | M6 | 2.85 | 2.85 € | http://www.ebay.de/itm/Stop-Muttern-Selbstsichernde-Stop-Muttern-Sicherungsmuttern-verzinkt-M3-M24-/282217367655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 | 20er Pack: Benötigt werden 16 => 1 Packung
1 | Sechskant Blechschrauben Bohrschrauben | 4,8mm x 38 mm | 7.40 € | 7.40 € | http://www.ebay.de/itm/Sechskant-Blechschrauben-Bohrschrauben-selbstschneidend-DIN-7504-3-5-6-3-mm/282380769780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 | 100er Pack: Benötigt werden 56 => 1 Packung
 |  |  |  | 18.70 € | keine Versandkosten
ebay - oscha0 | ebay.de
Stückzahl | Name | Größe | Preis/Stück | Gesamt | Link | Kommentar
1 | Senkkopfschrauben Edelstahl Innensechskant ISK DIN 7991 A2 VA V2A M3 - M12 | M4 - 25mm | 1.14 € | 1.14 € | http://www.ebay.de/itm/Senkkopfschrauben-Edelstahl-Innensechskant-ISK-DIN-7991-A2-VA-V2A-M3-M12-/282362954356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 | 50er Pack: Benötigt werden 12 => 1 Packung
1 | Senkkopfschrauben Edelstahl Innensechskant ISK DIN 7991 A2 VA V2A M3 - M12 | M6 - 100 mm | 28.37 € | 28.37 € | http://www.ebay.de/itm/Senkkopfschrauben-Edelstahl-Innensechskant-ISK-DIN-7991-A2-VA-V2A-M3-M12-/282362954356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 | 50er Pack: Benötigt werden 12 => 1 Packung
 | Versand |  |  | 3.90 €
 |  |  |  | 33.41 €
ebay - Sonstige Käufe | ebay.de
Stückzahl | Name | Größe | Preis/Stück | Gesamt | Link | Kommentar
1 | Kugellager 6201 ZZ | 1,2 cm x 3,2 cm x 1 cm | 7.50 € | 7.50 € | http://www.ebay.de/itm/Kugellager-6200-bis-6210-2RS-oder-ZZ-nach-Auswahl-Rillenkugellager-/261891435784?var= | 10er Pack: Benötigt werden 8 => 1 Packung
1 | Edelstahlrohr nahtlos Edelstahl 1.4301 Präzisionsrohr VA Rohr Länge 1000mm | AD: 8mm, ID: 6mm 1m | 14.93 € | 14.93 € | http://www.ebay.de/itm/Edelstahlrohr-nahtlos-Edelstahl-1-4301-Prazisionsrohr-VA-Rohr-Lange-1000mm-/191995756120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 | Hieraus werden 16 Spacer mit 6 cm. Preis ist mit Versand
1 | 4Axis Nema34 Stepper Motor 1232OZ-IN,5.6A DM860A Driver CNC Router | --- | 418.00 € | 418.00 € | http://www.ebay.de/itm/Germany-Ship-4Axis-Nema34-Stepper-Motor-1232OZ-IN-5-6A-DM860A-Driver-CNC-Router-/161689924837 | Set mit 4 Motoren und Ansteuerung | oder(falls angebot nicht mehr vorhanden): | http://www.ebay.de/itm/German-Ship-4axis-Stepper-Motor-Nema34-1232oz-in-5-6A-Driver-DM860A-CNC-Mill-/272828853051
16 | Trapezgewindemutter TR12x3 rechts 6kant SW 19x18 (3204) |  | 5.22 € | 83.52 € | http://www.ebay.de/itm/Trapezgewindemutter-TR12x3-rechts-6kant-SW-19x18-3204-/391491092767
2 | Gewindestift Kegelkuppe M2 M2,5 M3 M4 M5 M6 M8 | M3 - 4mm | 2.89 € | 5.78 € | http://www.ebay.de/itm/Gewindestift-Kegelkuppe-M2-M2-5-M3-M4-M5-M6-M8-Edelstahl-DIN913-Madenschraube-VA-/182584264805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 | 10er Pack: Benötigt werden 16 => 2 Packungen
 | Versand für Gewindestift |  |  | 0.95 €
4 | Coupler 12mm - 14mm | D30 L 42 | 8.51 € | 34.04 € | http://www.ebay.de/itm/BF-12mm-X-14mm-CNC-Flexible-Plum-Coupling-Shaft-Coupler-D30L42-CMY-/391402327366
4 | M5 Gewindestange | M5 1m | 1.00 € | 4.00 € | http://www.ebay.de/itm/Gewindestange-A2-V2A-Niro-Edelstahl-DIN-975-976-Gewindestangen-1000-mm-1m-Meter-/271358495006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 | 2 m Gewindestange. 1 m könnte zu knapp werden
 | Versand für Gewindestange |  |  | 3.85 €
1 | ER16 1,5KW FRÄS SPINDEL LUFTGEKÜHLTE |  | 227.20 € | 227.20 € | http://www.ebay.de/itm/ER16-1-5KW-FRAS-SPINDEL-LUFTGEKUHLTE-AIR-COOLED-MOTOR-FREQUENZUMRICHTER-VFD-/272351352143
1 | Geeetech Extruder MK8 3D |  | 27.98 € | 27.98 € | http://www.ebay.de/itm/SHIPPING-FROM-Germany-Extruder-MK8-3D-Drucker-prusa-Mendel-den-I3-Drucker-/322294442290 | Mit Versand
1 | Netzteil 12V-10A |  | 16.76 € | 16.76 € | http://www.ebay.de/itm/DC12V-2A-30A-Netzteil-Trafo-Adapter-Treiber-Power-Supply-LED-Strip-Leiste-Lampe-/162296585279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
1 | 50 Drop in T-Nuts M5 |  | 4.80 € | 4.80 € | https://www.ebay.de/itm/50PCS-20-Serie-europaeischen-T-Nut-Aluminium-Carbon-Steel-Drop-In-T-Nut-M5/182107289895
1 | 50 M4 Schrauben 30 mm |  | 4.45 € | 4.45 € | https://www.ebay.de/itm/M4-DIN-912-Zylinderschraube-Innensechskant-Zylinder-Kopf-Schrauben-verzinkte-M4x/371556859648
1 | 20 Stopmuttern M4 x 0,7/7 |  | 3.15 € | 3.15 € | https://www.ebay.de/itm/Stop-Muttern-Selbstsichernde-Stop-Muttern-Sicherungsmuttern-verzinkt-M3-M24/282217367655
1 | 2x Mosfet Anet A8 |  | 18.99 € | 18.99 € | https://www.ebay.de/itm/2x-Mosfet-Anet-A8-A6-A2-12v-Ramps-3D-Printer-Drucker-Rep-Heatbed-Rap-Prusa-i3/263509259787
1 | Motortreiber |  | 6.20 € | 6.20 € | https://www.ebay.com/itm/CNC-Single-Axis-TB6600-0-2-5A-Two-Phase-Hybrid-Stepper-Motor-Driver-Controlle/112940300350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
1 | 2x CTC K-type Temperatur Sensor |  | 10.55 € | 10.55 € | https://www.ebay.de/itm/2x-CTC-K-type-Temperature-Sensor-Thermocouple-Shielded-For-CTC-3D-Printer/282897974125
2 | 10x Set Aluminum Winkel |  | 2.03 € | 4.06 € | https://www.ebay.de/itm/10x-Set-Aluminum-2020-Corner-Fitting-90-Angle-Part-20-20mm-Connector-Bracket-RE/162822503983
1 | Mounting Plate Extruder |  | 1.99 € | 1.99 € | https://www.ebay.de/itm/Geeetech-All-Metal-MK8-Extruder-mount-plate-for-single-MK8-Prusa-I3-3D-Printer/282162581885
2 | Spindle Mounts |  | 27.69 € | 55.38 € | https://www.ebay.de/itm/80mm-Durchmesser-Spindle-Mount-Bracket-Clamp-Halter-mit-2Schraube-for-CNC-Motor/123035787996
1 | 20 cm Male Female Jumperwire |  | 4.79 € | 4.79 € | https://www.ebay.de/itm/DE-40Pin-Dupont-Kabel-Jumper-Wire-Linie-Kit-Pi-Arduino-Breadboard-M-F-M-M-F-F/282967860313
1 | Arduino DUE |  | 20.90 € | 20.90 € | https://www.ebay.de/itm/DUE-Entwicklungsboard-R3-32-Bit-ARM-Cortex-M3-Arduino-Kompatibel/201501802020
2 | DC-DC 5v 6v 9v 12v 15v 24v adjustable Linear Step Down Voltage |  |  | 1.00 € | https://www.ebay.de/itm/DC-DC-5v-6v-9v-12v-15v-24v-adjustable-Linear-Step-Down-Voltage-Regulator-Module/122879104236
1 | Präzisions Optokoppler Sharp PC817 |  |  | 5.89 € | https://www.ebay.de/itm/Prazisions-Optokoppler-Sharp-PC817-DIL4-5-10-25-50-oder-100-Stuck/332326198645
1 | Analog 10V Panelmeter | 100 x 80 x 12mm |  | 6.03 € | https://www.ebay.de/itm/Messung-Tool-Analog-Panel-Voltmeter-DC-0-10V-Messbereich/352027038145?epid=1743592569
3 | M12 Gewindestange | M12 1m | 3.13 € | 9.39 € | https://www.ebay.de/itm/Gewindestange-A2-V2A-Niro-Edelstahl-DIN-975-976-Gewindestangen-1000-mm-1m-Meter-/271358495006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 | Verstärkung der Z-Achse
25 | M12 Stopmuttern | M12 1m | 9.45 € | 9.45 € | https://www.ebay.de/itm/Stopmutter-Sicherungsmuttern-DIN985-Edelstahl-VA-M2-M3-M4-M5-M6-M8-M12-Polystop/301329119935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
 |  |  |  | 1011.53 € | zzgl. Versand
 |  |  | Gesamter Betrag: | 2327.19 €
 |  |  | Momentan fehlen noch Arduino, Verkabelung, Schleppketten und Glasbett.
 |  |  | Ich habe dies bewusst weggelassen, es einfacher wird dies zu bemessen, wenn es einmal so weit ist.

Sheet: Tabelle1
Kostenvoranschlag - MINT CNC-Fräse
Stückzahl | Name | Größe | Preis/Stück | Gesamt | Link | Kommentar
7 | V-Slot® Linear Rail | 2cm x 8 cm x 150 cm | 25.11 € | 175.77 € | http://openbuildspartstore.com/v-slot-linear-rail/ | 5 davon müssen auf 125 cm gekürzt werden - alles in silber
6 | V-Slot® Linear Rail | 2cm x 8 cm x 50 cm | 8.37 € | 50.22 € | http://openbuildspartstore.com/v-slot-linear-rail/ | silber
3 | C-Beam® Linear Rail | 4cm x 8 cm x 150 cm | 32.65 € | 97.95 € | http://openbuildspartstore.com/c-beam-linear-rail/ | silber - hier gibt es keine auswahl
4 | V-Slot® Linear Rail | 2 cm x 4 cm x 50 cm | 5.44 € | 21.76 € | http://openbuildspartstore.com/v-slot-linear-rail/ | silber - die müssen wir in der Schreinerei halbieren - ist billiger als 25cm
68 | Cast Corner Bracket | 2 cm x 2 cm x 1,7 cm | 1.26 € | 85.68 € | http://openbuildspartstore.com/cast-corner-bracket/
124 | Low Profile Screws M5 | M5 - 8 mm | 2.51 € | 311.24 € | http://openbuildspartstore.com/low-profile-screws-m5/ | Werden in 25er Packungen verkauft!!!
350 | Tee Nuts (25 Pack) | M5 | 4.14 € | 1449.00 € | http://openbuildspartstore.com/tee-nuts-25-pack/ | Werden in 25er Packungen verkauft!!!
12 | 90 Degree Joining Plate | 6 cm x 6 cm x 0,4 cm | 4.02 € | 48.24 € | http://openbuildspartstore.com/90-degree-joining-plate/
64 | Low Profile Screws M5 | M5 - 10 mm | 2.68 € | 171.52 € | http://openbuildspartstore.com/low-profile-screws-m5/
56 | Self Tapping Screw | M5 - 3/4" | 0.21 € | 11.76 € | http://openbuildspartstore.com/self-tapping-screw/ | werden tatsächlich einzeln verkauft
4 | 3 Hole Joining Strip Plate | 6 cm x 1,8 cm x 0,4 cm | 1.72 € | 6.88 € | http://openbuildspartstore.com/3-hole-joining-strip-plate/
4 | T Joining Plate | 6 cm x 6 cm x 0,4 cm | 3.89 € | 15.56 € | http://openbuildspartstore.com/t-joining-plate/
8 | Aluminium Blech hochfest (7075) 8 mm Stark Zuschnitt frei wählbar | 15 cm x 15 cm x 0,8 cm | 6.00 € | 48.00 € | http://www.ebay.de/itm/Aluminium-Blech-hochfest-7075-8-mm-Stark-Zuschnitt-frei-wahlbar-/111645652297?var= | Ist AlZnMgCu1,5 => hart, aber gut zu fräsen. Es kommen noch 5 euro Versand hinzu
94 | Low Profile Screws M5 | M5 - 20mm | 2.85 € | 267.90 € | http://openbuildspartstore.com/low-profile-screws-m5/ | 25er Pack
8 | Kugellager 6201 ZZ | 1,2 cm x 3,2 cm x 1 cm | 7.50 € | 60.00 € | http://www.ebay.de/itm/Kugellager-6200-bis-6210-2RS-oder-ZZ-nach-Auswahl-Rillenkugellager-/261891435784?var= | 10er Pack
1 | Edelstahlrohr nahtlos Edelstahl 1.4301 Präzisionsrohr VA Rohr Länge 1000mm | AD: 8mm, ID: 6mm 1m | 14.93 € | 14.93 € | http://www.ebay.de/itm/Edelstahlrohr-nahtlos-Edelstahl-1-4301-Prazisionsrohr-VA-Rohr-Lange-1000mm-/191995756120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 | 16 | Preis mit Versand
1 | Senkkopfschrauben Edelstahl Innensechskant ISK DIN 7991 A2 VA V2A M3 - M12 | M6 - 100 mm | 32.27 € | 32.27 € | http://www.ebay.de/itm/Senkkopfschrauben-Edelstahl-Innensechskant-ISK-DIN-7991-A2-VA-V2A-M3-M12-/282362954356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 | 50er Pack - 8 + 4 + 4 | Preis mit Versand
1 | 4Axis Nema34 Stepper Motor 1232OZ-IN,5.6A DM860A Driver CNC Router | --- | 418.00 € | 418.00 € | http://www.ebay.de/itm/Germany-Ship-4Axis-Nema34-Stepper-Motor-1232OZ-IN-5-6A-DM860A-Driver-CNC-Router-/161689924837 | sind 4 motoren | oder(falls angebot nicht mehr vorhanden): | http://www.ebay.de/itm/German-Ship-4axis-Stepper-Motor-Nema34-1232oz-in-5-6A-Driver-DM860A-CNC-Mill-/272828853051
1 | MDF Platte | 150 cm x 125 cm x 1,9 cm |  | 0.00 € | Schreinerei
1 | OSB Platte | 141 cm x 54 cm x 1,9 cm |  | 0.00 € | Schreinerei
56 | Low Profile Screws M5 | M5 - 25 mm | 3.14 € | 175.84 € | http://openbuildspartstore.com/low-profile-screws-m5/ | 25er Pack
5 | C-Beam® Gantry Plate - XLarge |  | 12.51 € | 62.55 € | http://openbuildspartstore.com/c-beam-gantry-plate-xlarge/
1 | Stop-Muttern Selbstsichernde | M6 | 2.85 | 2.85 € | http://www.ebay.de/itm/Stop-Muttern-Selbstsichernde-Stop-Muttern-Sicherungsmuttern-verzinkt-M3-M24-/282217367655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 | 16 | 20er Pack bis jetzt
4 | TR12 ACME Trapezoidal POM NUT |  | 13.67 € | 54.68 € | https://snbinc.ca/store/products.php?110&currency=USD&sid=d84fa16a50b4d94e553285ea92b13391 | Ausland - Preis in Dollar
1 | Senkkopfschrauben Edelstahl Innensechskant ISK DIN 7991 A2 VA V2A M3 - M12 | M4 - 25mm | 5.04 € | 5.04 € | http://www.ebay.de/itm/Senkkopfschrauben-Edelstahl-Innensechskant-ISK-DIN-7991-A2-VA-V2A-M3-M12-/282362954356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 | 50er Pack - 8 + 4 + 4 | Preis mit Versand
1 | Stop-Muttern Selbstsichernde | M4 | 2.85 € | 2.85 € | http://www.ebay.de/itm/Stop-Muttern-Selbstsichernde-Stop-Muttern-Sicherungsmuttern-verzinkt-M3-M24-/282217367655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 | 20er Pack - 8 + 4 + 4 | Preis mit Versand
4 |  |  |  | 0 |  |  | Aluteile 15mm dick zum Fräsen
2 | Stop-Muttern Selbstsichernde | M5 | 2.80 € | 5.60 € | http://www.ebay.de/itm/Stop-Muttern-Selbstsichernde-Stop-Muttern-Sicherungsmuttern-verzinkt-M3-M24-/282217367655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 | 20er Pack - 4 + 12 + 10 + 2
12 | Low Profile Screws M5 | M5 - 45 mm | 3.98 € | 47.76 € | http://openbuildspartstore.com/low-profile-screws-m5/ |  | 25er Pack
32 | Xtreme Solid V Wheel™ Kit |  | 5.65 € | 180.80 € | http://openbuildspartstore.com/xtreme-solid-v-wheel-kit/
32 | Aluminum Spacers | 20mm | 0.29 € | 9.28 € | http://openbuildspartstore.com/aluminum-spacers/
12 | Low Profile Screws M5 | M5 - 15 mm | 2.76 € | 33.12 € | http://openbuildspartstore.com/low-profile-screws-m5/ | 25er Pack
3 | Trapezgewindespindel TR 12x3 Rechts | 1601mm - 1700mm | 13.34 € | 40.02 € | http://www.ebay.de/itm/Trapezgewindespindel-TR-12x3-Rechts-/192252502309?var= | Können doch schon mit 1,6 m gekauft werden | gemeinsam dann 6,7€ versand
1 | Trapezgewindespindel TR 12x3 Rechts | 801mm - 900mm | 9.09 € | 9.09 €
16 | Trapezgewindemutter TR12x3 rechts 6kant SW 19x18 (3204) |  | 5.22 € | 83.52 € | http://www.ebay.de/itm/Trapezgewindemutter-TR12x3-rechts-6kant-SW-19x18-3204-/391491092767
2 | Gewindestift Kegelkuppe M2 M2,5 M3 M4 M5 M6 M8 | M3 - 4mm | 3.84 € | 7.68 € | http://www.ebay.de/itm/Gewindestift-Kegelkuppe-M2-M2-5-M3-M4-M5-M6-M8-Edelstahl-DIN913-Madenschraube-VA-/182584264805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 | 10er Pack - 16
4 | Coupler 12mm - 14mm | D30 L 42 | 8.51 € | 34.04 € | http://www.ebay.de/itm/BF-12mm-X-14mm-CNC-Flexible-Plum-Coupling-Shaft-Coupler-D30L42-CMY-/391402327366
8 | Aluminium Blech hochfest (7075) 8 mm Stark Zuschnitt frei wählbar | 10 cm x 10 cm x 0,8 cm | 2.67 € | 21.36 € | http://www.ebay.de/itm/Aluminium-Blech-hochfest-7075-8-mm-Stark-Zuschnitt-frei-wahlbar-/111645652297?var= | Eigentlich nur 9,5cm, aber wenn es ein bisschen größer ist, ist egal
10 | Aluminum Spacers | 9mm | 0.21 € | 2.10 € | http://openbuildspartstore.com/aluminum-spacers/
2 | M5 Gewindestange | M5 1m | 1.00 € | 2.00 € | http://www.ebay.de/itm/Gewindestange-A2-V2A-Niro-Edelstahl-DIN-975-976-Gewindestangen-1000-mm-1m-Meter-/271358495006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 | 2 m Gewindestange. 1 m könnte zu knapp werden | + 3,85€ Versand
8 | Precision Shim - 10x5x1mm | 10x5x1mm | 0.21 € | 1.68 € | http://openbuildspartstore.com/precision-shim-10x5x1mm/
1 | C-Beam® Linear Rail | 4cm x 8 cm x 100 cm | 23.44 € | 23.44 € | http://openbuildspartstore.com/c-beam-linear-rail/ | silber - hier gibt es keine auswahl
28 |  |  |  | 0.00 €
 |  |  |  | 0.00 €
 |  |  |  | 0.00 €

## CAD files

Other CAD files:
Motormounts-dxf/Z-Achse - Motormount hinten II.dxf
Motormounts-dxf/Y-Achse _ Motormount II.dxf
Motormounts-dxf/Bein links - Motormount hinten II.dxf
Motormounts-dxf/Bein rechts - Motormount hinten I.dxf
Motormounts-dxf/Bein rechts - Motormount hinten II.dxf
Motormounts-dxf/Bein links - Motormount hinten I.dxf
Motormounts-dxf/Z-Achse - Motormount hinten I.dxf
Motormounts-dxf/Y-Achse _ Motormount I.dxf
CAD-files/CNC-Mill-v3 v20.f3d

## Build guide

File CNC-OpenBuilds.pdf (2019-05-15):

# OPEN SOURCE LARGE FORMAT CNC-MACHINE & 3D-PRINTER

### David Koch, Sebastian Schütz & Stefan Schütz

2019

1

## Content

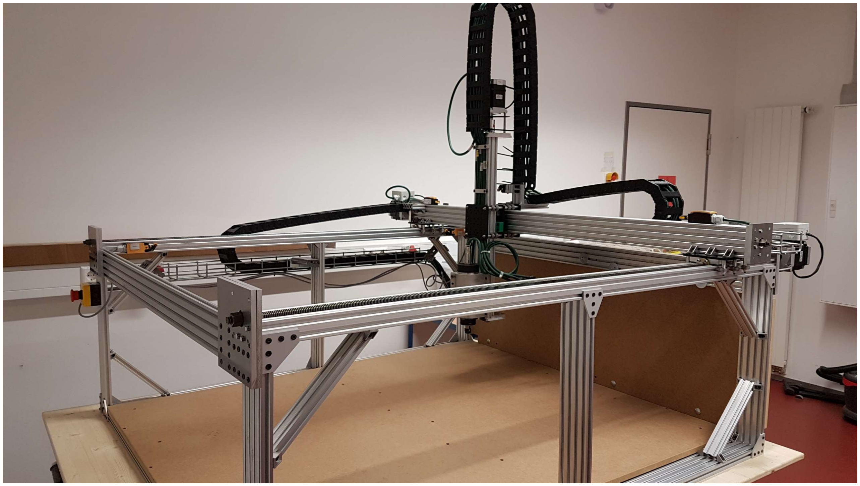
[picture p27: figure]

2

Figure 1: Current state of the machine

## 1. Introduction

On our school “Birklehof” in Germany, we were offered the possibility to submit a project to the program “Micro-Maro-Mint” of the “Baden-Württemberg-Stiftung” (Baden-Wuerttemberg-Foundation). The “Micro-Macro-Mint”-program supports students interested in mathematics, informatic or engineering with up to 2500€ for their projects. After submitting our application with a first 3D-Model and a Bill of material, we got the funding.

Our goal was to build a large format CNC-machine, with the money available. Due to limited access to a machine shop, we had to rely mostly on screwed connections. This led to the design decision of using aluminium extrusions. The Open Build rails seemed like a perfect fit for our project.

Furthermore we added the option to use the machine as a giant 3D-printer. The wires for the extruder, a stepper motor driver and a sufficient power supply are already installed in the electrical cabinet.

To make this project as open source as possible we used the open builds platform and an Arduino Due with TinyG2 core as controller.

## 2. General information

The current state of the machine (without the additional Y-axis):

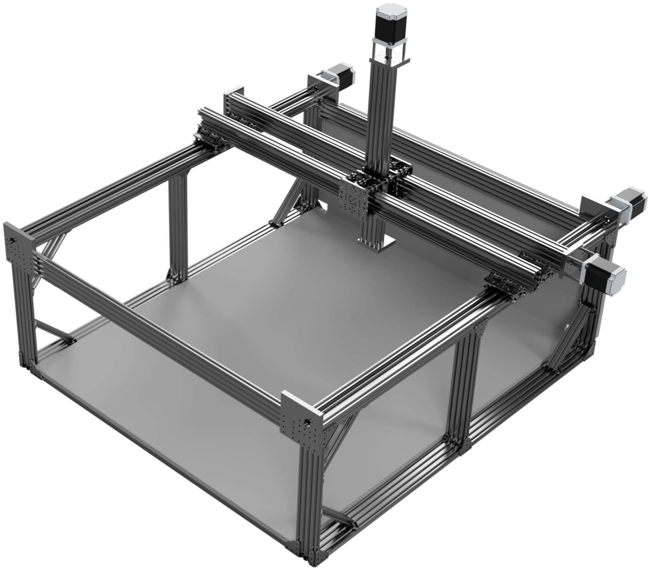
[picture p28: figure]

3

Figure 2: Final Rendering

The final form:

The current version isn´t behaving according to plan, so we had to do some design tweaks, which should solve these problems. In the section Issues we will talk about those.

The total size of the machine is roughly:

- X: 172 cm
- Y: 172 cm
- Z: 128 cm
- This measurements are measured up to the outer most endpoints. For reference, the MDFplate on the bottom of the machine measures 150 cm by 125cm. The cable chains are not taken into account

The milling area boils down to:

4

- X: 116,8 cm
- Y: 112,5cm
- Z: 16,5 cm

While maintaining a weight of ca. 200 kg.

## 3. Design choices

### 3.1 Power

A detailed description can be found under Wiring Diagram. First things first. We chose to use three phase power. This is wildly available in Germany, so there should be no problems. We did this, because the maximum power output from a normal single phase outlet is about 230V at 16 Amps, which gives you roughly 3680 watts. Considering the four 350 Watt power bricks for the stepper motors and the 1,5 kW spindle, this could get us pretty close to the limit. So we split the main parts over the three phases. On for the spindle, one for the stepper motors and one for the controller and the 3D-printing part. This is also helping to reduce interferences.

### 3.2 Open Build V-wheels

Our goal was to drive costs down, which was the reason, why
we decided to use the V-wheels. Furthermore the lack of a proper machine shop forces us to rely on as many screwed connections as possible, so aluminium extrusions with an integrated linear rail system just came in handy.

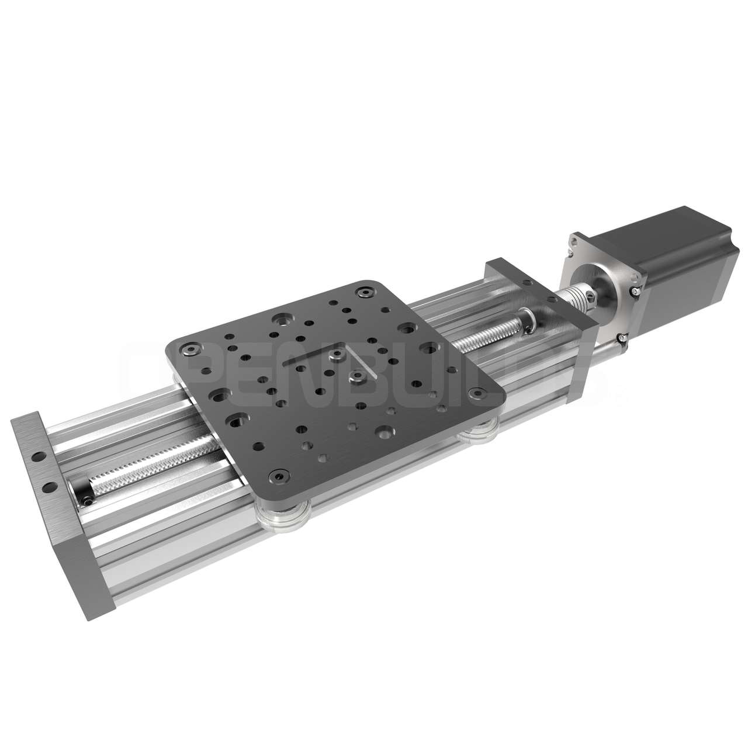
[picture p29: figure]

The design for the x-axis was borrowed form the linear actuators in the open build store. But the load on the wheels in this design is too high, so the won´t turn properly. In the rendering of the final version you can see, that we decided to add an additional Y-axis to spread the load onto more wheels.

Figure 3: https://openbuildspartstore.com/c-beam-xlargelinear-actuator-bundle/

### 3.3 Motors with Trapezoidal Screws

The stepper motors are NEMA 34 stepper motors with 1232OZ/IN and the 5.6A DM860A drivers. We bought one of these 4 Axis-kits out of china and are quite happy with it. The motors are mounted to our custom motor mounts and are connected to the trapezoidal screws with a normal 12 to 14 mm coupler. The used trapezoidal screws are 12 mm in diameter and have a pitch of 3mm. We decided to use these, because we couldn´t get any ball screws in the desired length with this diameter. The main problem was, that all nuts for screws over 12 mm in diameter were to big to be used inside the C-beams.

Figure 3: Design template

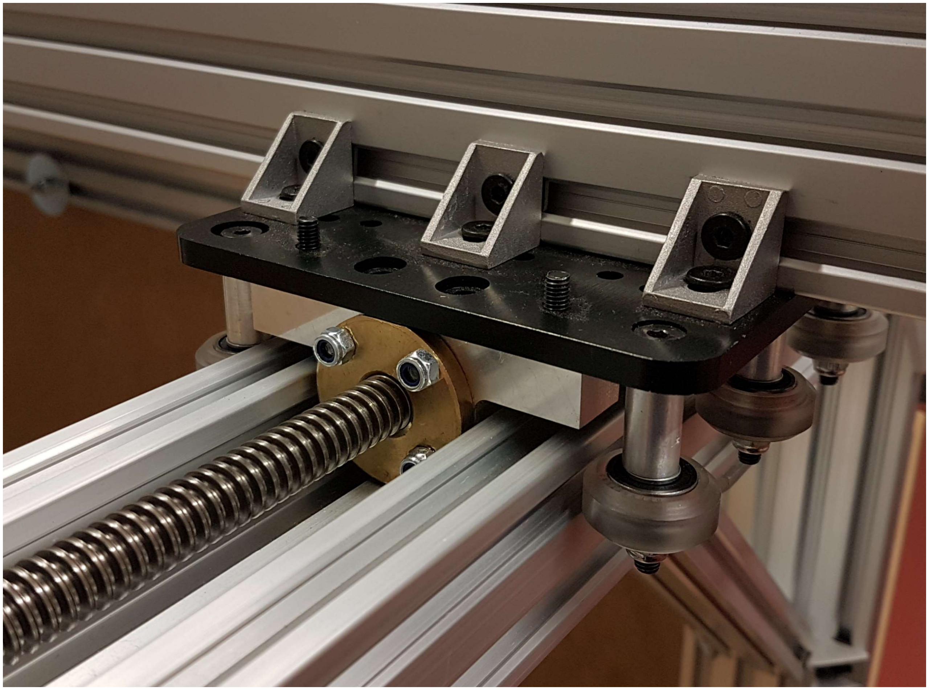
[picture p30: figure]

5

Figure 4: The holder for the nuts
As you can see in picture four, the space inside the C-beam is filled out by the holder for the nut. The holder was machined on our modified Esel EP 1090 (it now runs on grbl). So 12mm was the
maximum we could pack into a c-beam. In hindsight we probably should have used ACME-Screws with the same diameter.

The motor current on the drivers is set to the maximum of 7,8 Amps

1 | 2 | 3
OFF | OFF | OFF
and Microstepping is set to 2.
5 | 6 | 7 | 8
ON | ON | ON | ON

### 3.4 Controller board

The machine is running of TinyG2core version 101. It runs on an Arduino due. All outputs and inputs of the Due are protected via Optocouplers. These furthermore serve as level shifters. The connections are all following the wiring suggested on the official wiki page of tinyG2 and can also be found in the Wiring Diagram. Due to the sad fact, that the Due doesn´t have an EEPROM, we have to send all commands on every startup. Here is the list of the current configuration:

6

$ej=0 //Enable text mode
$1mi=2 //Microstepping: 2
$2mi=2
$3mi=2
$1tr=3 //Travel per Revolution: 3mm $2tr=3
$3tr=3
$lim=1// activate limit switches

$di1mo=1 // Xmin limit switch activated. Set to active hi (NC) $di1ac=1 // Stop when hit
$di1fn=1 // Use as limit switch
$di2mo=1 ; Xmax
$di2ac=1
$di2fn=1

$di3mo=1 ; Ymin
$di3ac=1
$di3fn=1
$di4mo=1 ; Ymax
$di4ac=1
$di4fn=1

$di5mo=2 ; Zmin - disabled $di5ac=0
$di5fn=0
$di6mo=1 ; Zmax
$di6ac=1
$di6fn=1

$xsv=500 // 500mm/min homing speed $ysv=500
$zsv=500

$xtm=1168 //Max travel X-axis $ytm=1125
$ztm=165

We are running it with CNCjs and had no problems till now. Every command entered will be validated. We use the left USB-Port on the DUE and it will show up as a Microsoft Serial USB-device.

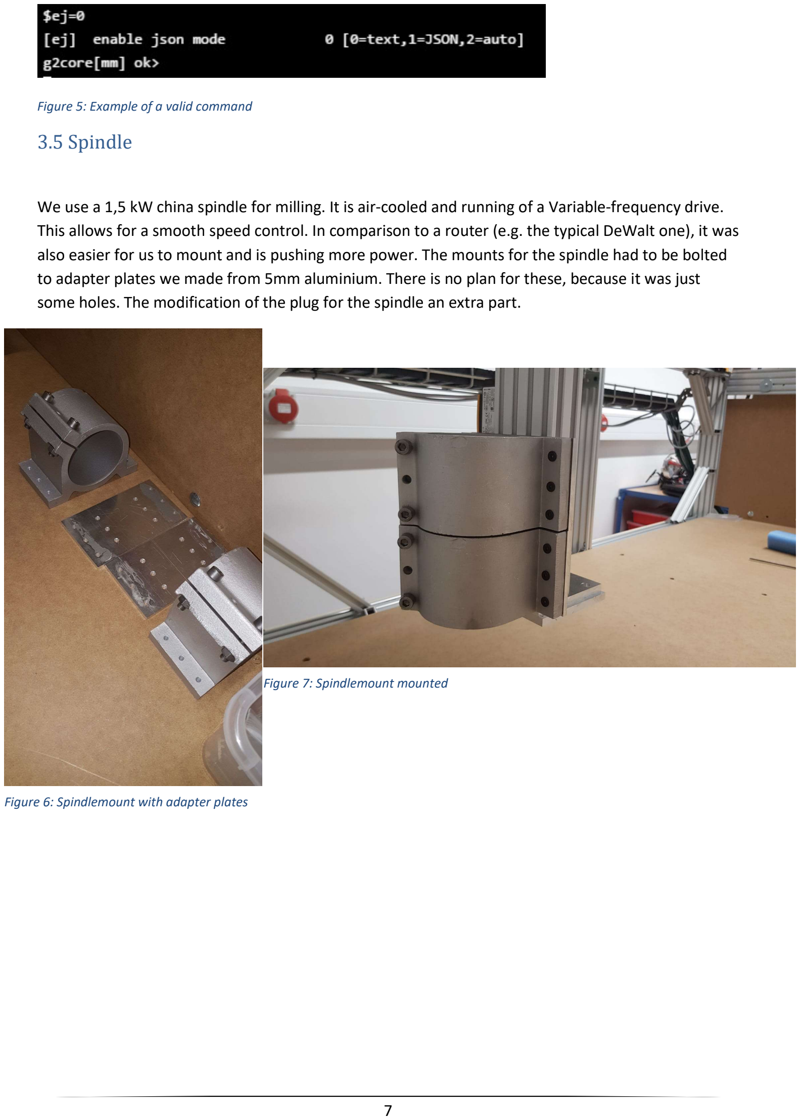
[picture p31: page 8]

7

Figure 6: Spindlemount with adapter plates

Figure 7: Spindlemount mounted

Figure 5: Example of a valid command

### 3.5 Spindle

We use a 1,5 kW china spindle for milling. It is air-cooled and running of a Variable-frequency drive. This allows for a smooth speed control. In comparison to a router (e.g. the typical DeWalt one), it was also easier for us to mount and is pushing more power. The mounts for the spindle had to be bolted to adapter plates we made from 5mm aluminium. There is no plan for these, because it was just some holes. The modification of the plug for the spindle an extra part.

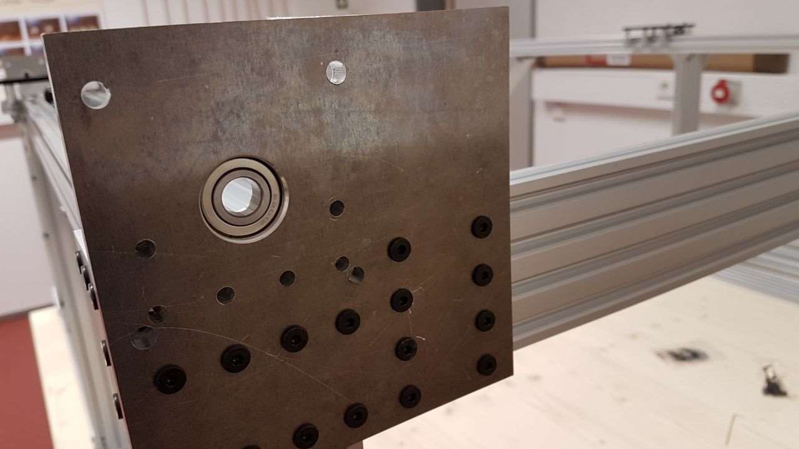
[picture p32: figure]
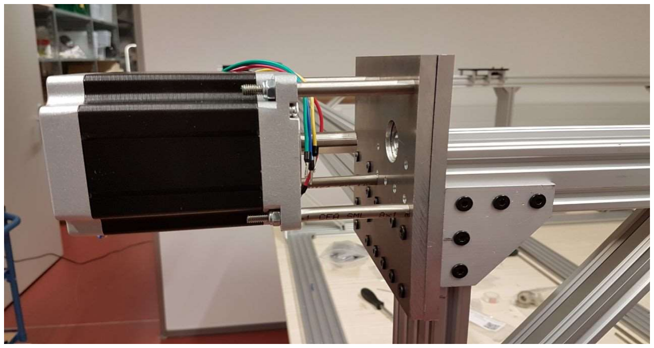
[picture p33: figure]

8

### 3.6 Motor mounts

The motor mounts are custom designed and machined. We made them on our modified ESEL EP 1090 (running of GRBL).

Figure 8: The motor mount without motor
As you can see in the picture they actually serve three purposes:

### 1. They are connecting elements in the frame

2. The bearings take axial load out form the trapezoidal screw, so that it doesn’t destroys the bearings in the motor. In hindsight we learned from a “This Old Tony”-video¹
, that there exist
tapered roller bearings, which would have been the better choice here.
3. They hold the motors. The motors are mounted with a 5mm threaded rod inside a stainless steel tube.

1 https://youtu.be/HYOgmhpBUJs?t=277 Figure 9: The motor mounted with the stainless steel tubes

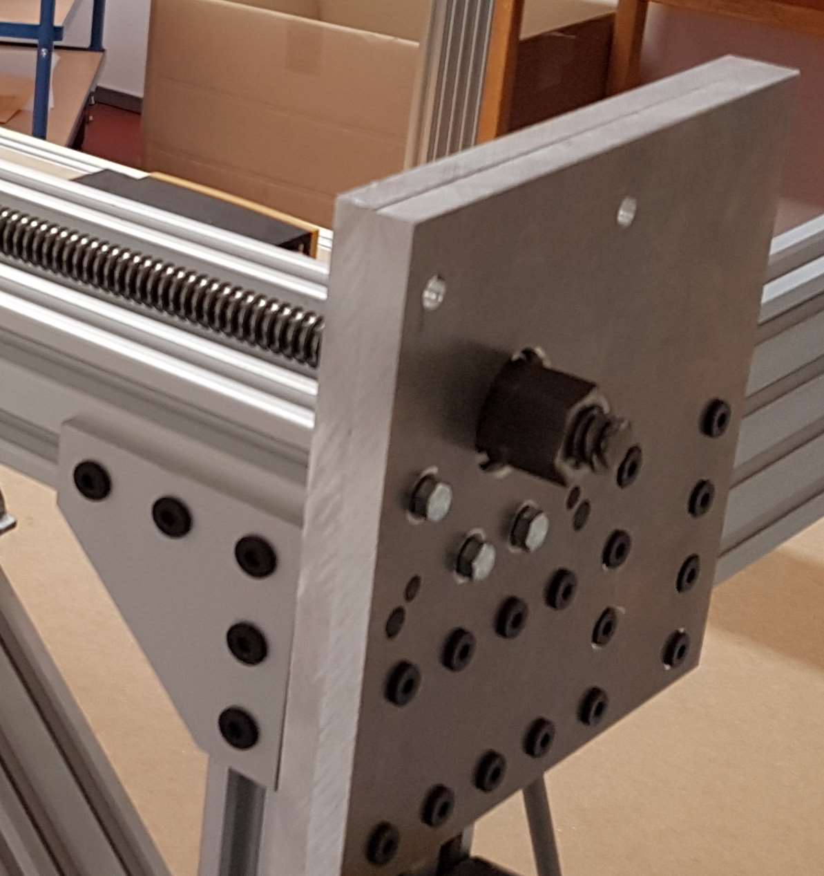
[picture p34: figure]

9

Figure 10: attachment of the TR12-3 screw

This design allowed us to cheat a little bit and saved us the headache of machining a fitting faceplate for the motor. One additional improvement apart from the tapered roller bearings would be to put a screw through the top part of the motor mount. In the picture is seems like the two aluminium plates would be separating, but in reality it is not as bad.

The bearings take the axial load, because we bought nuts for the trapezoidal screw, took one side drilled a small hole and cut a thread for M3 grub screws. The nuts sit one both sides of the bearing and also on the end, where the motor is mounted.

### 3.7 Overall design

We went with a cage like design and till now, it has served as well. We were able to get a surprising amount of precision with the aluminium extrusions. The deviation on the X-Rails is mostly down to measurement errors. The added MDF plates add an additionally stability, especially the backplate, and serve as a waste board.

## 4. Plans

### 4.1 CAD-Design

The design was done in Fusion 360. I exported the model to every format, the export window offered, so that there are no problems with different CAD solutions. Furthermore here is the link, you can use to download the model from Autodesk: http://a360.co/2y7nwAO This should give you the most current version.

10

### 4.2 Wiring Diagram

The electrical part of the machine is complying with the following regulations:

- 2006-42-EG Maschinenrichtlinie
- BGI5003 Maschinen der Zerspannung
- DIN EN 60204 Elektrische Ausrüstung von Maschinen

Here we got some support form the father of Stefan and Sebastian. The whole construction was done in ePlan P8.

The controls consist of two thermostat controlled ventilated electrical cabinets. One for the Variable-frequency drive of the spindle and one for the actual controls. In the second one are the power supplies, the drivers for the stepper motors, the power supply for the extruder and the Arduino DUE. The USB-port of the DUE is expanded to outside of the cabinet, so that the machine can be run with the cabinets closed.

The extra cabinet for the variable-frequency drive was done due to EMC reasons, so that it wouldn´t interfere with the low voltage signals from the Arduino. The parameters for the variable-frequency drive were taken from this very useful site: http://www.rchobby-net.de/fraese

The cables and the cable chains were provided by Igus²
. The used cables are mostly shielded and are designed to be used inside cable chains.

All end positions on the X, Y, and Z-axis are equipped with safety limit switches (Normally closed), which are galvanic isolated through optocouplers, before the signals are interpreted by the Arduino DUE. In order to make the limit switches more resistant to interferences we are using a 12V signal instead of the 3,3V signal which would normally be provided by the Arduino.

### 2 https://www.igus.de/

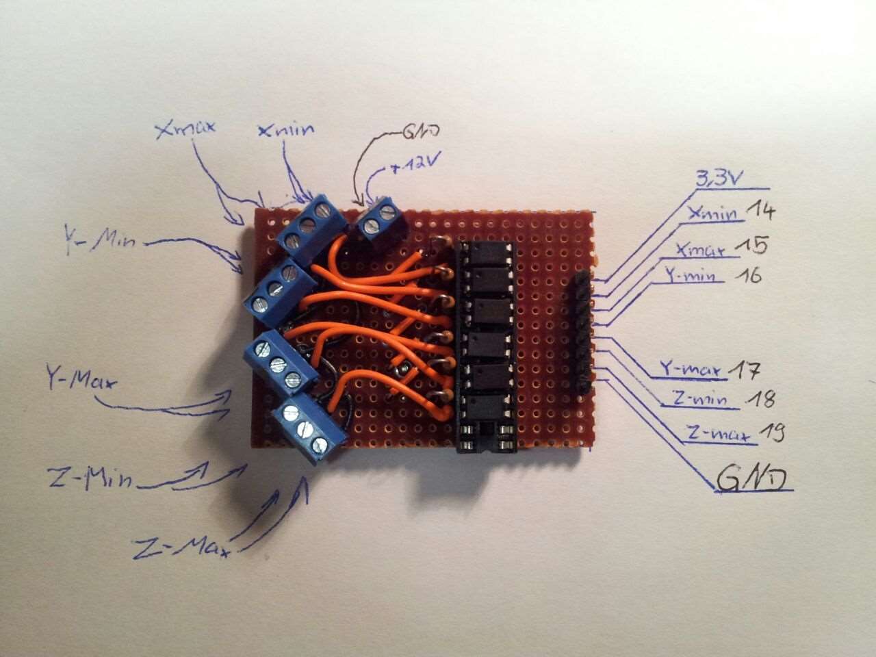
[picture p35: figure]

11

Figure 11: The optocoupler circuit board
The CNC is equipped with two emergency stops, which isolate the machine from main voltage. The Arduino and the optocoupler board are the only ones, which are still provided with their 12V power. There is an additional off-switch, which turns off the machine completely.

The controls for the machine are in the door of the electrical cabinet.

On the larger cabinet are:

- On/Off
- Spindle on/off
- Extruder on/off
- Emergency stop
- Off-Switch

And the smaller on:

- Speed
- Clockwise/0/anti-clockwise rotation

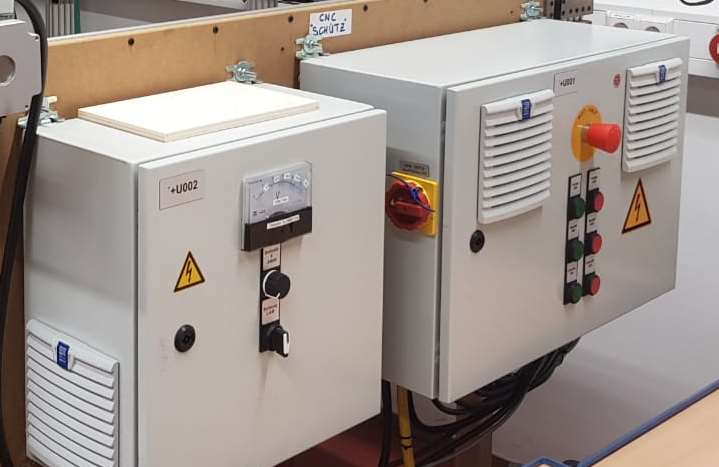
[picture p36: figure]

12

Figure 12: The controls for one/off, ...
The speed control is done with a 10kΩ potentiometer and a 0-10V analog display, where 10V equals 24000 rpm.

After completion the machine was tested according to the regulations by an electrical engineer.

### 4.3 BOM

The current BOM states 2.308,35 €. In this calculation are not included:

- The wooden plates on the back and the bottom of the machine
- The COMPLETE wiring, because we were sponsored (~1000€. You could cut the price by using cheaper hardware/no-name electronics):
o Cable cabinets
o Wiring for the cable chains
o Cable chains with fitting mounts
o Small electric parts (switches, relays, etc. what goes into the electrical cabinet)
- An optional glass bed for using the machine as a 3D-printer

The nuts we used to connect the trapezoidal screw with the C-beam gantry plate also went up significantly in price. We had some with 4 holes in them, but can´t find them anymore. The measurements for our nuts are:

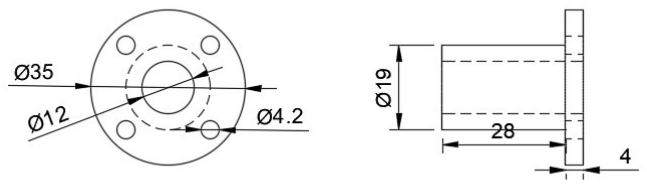
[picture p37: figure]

13

Figure 13: The used nuts. [mm]

### 4.4 Manual and Instructions (kind of)

The document “Aufbauanleitung.pdf” contains pictures from the CAD-Model and some tips, how you could build the CNC. Just to be clear: This isn´t a perfect manual. For example we never added mounts for the cable chains and improvised them. So you should feel comfortable doing such a big project. For reference: The mechanical construction alone took over 100h man-hours. The wiring inside the electrical cabinets plus laying the cables inside the cable chains and hooking them up to their destinations took approximal another 60h. So this is not a weekend project.

## 5. Construction

### 5.1 Modification of the spindle

Due to using the inside the maker scene popular china spindle, we realised that the motor is equipped with a CE-certification, but the used 4-pole plug didn´t have a ground wire connected to the metal frame. Furthermore, could be assumed that the used plug only was suitable for lowvoltage applications (~60V). To solve these problems, we added a ground connection to the metal frame and changed the plug to a sufficient M17-high power plug rated for 690V at 23A.

The rpm can be controlled between 4000 and 24000 rmp.

### 5.2 Machining of the custom parts

We had two custom parts. One there the motor mounts and the other was the holder for the nuts. We machined both on our ISEL EP1090 with a 6mm and 3mm bit out of aluminium.

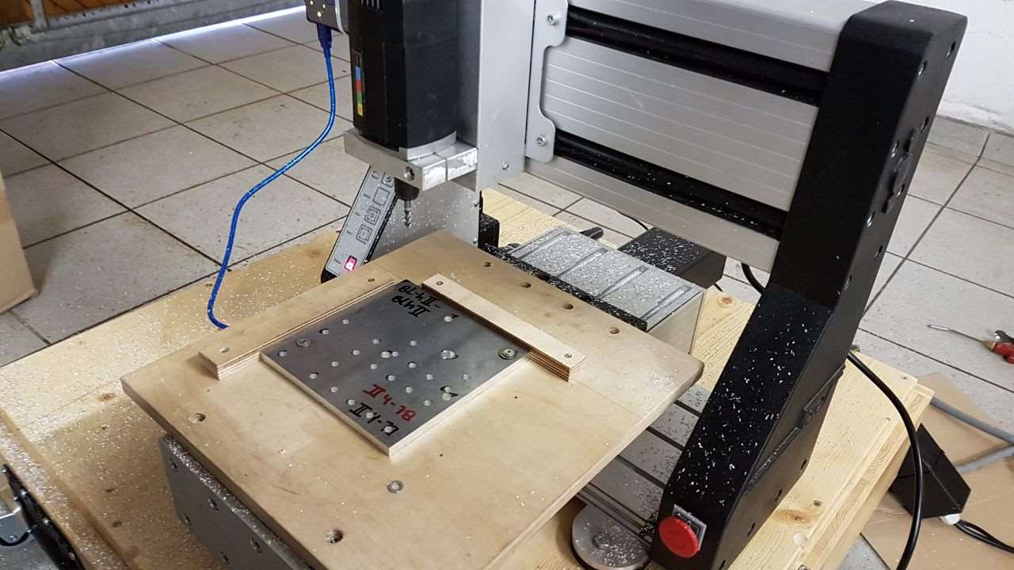
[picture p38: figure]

14

Figure 14: Preparation for machining

We had to machine 16 aluminium plates, but we designed the mounts in a way, so that we only needed 8 files and could use them twice:

- 2x Motormount hinten I | (links)
- 2x Motormount hinten II | (links)
- 2x Motormount hinten I | (rechts)
- 2x Motormount hinten II | (rechts)
- 2x Motormount I | (Y)
- 2x Motormount II | (Y)
- 2x Motormount I | (Z)
- 2x Motormount II | (Z)

All those files are added. They are 3D-DXFs. If they don´t work for you, you can still take the mounts from the 3D model.

Always two plates of the motor mount go together and sandwich on of the bearings in between them.

The holder for the nuts war pretty simple. The hole connecting the holder to the C-beam gantry plate was drilled by hand.

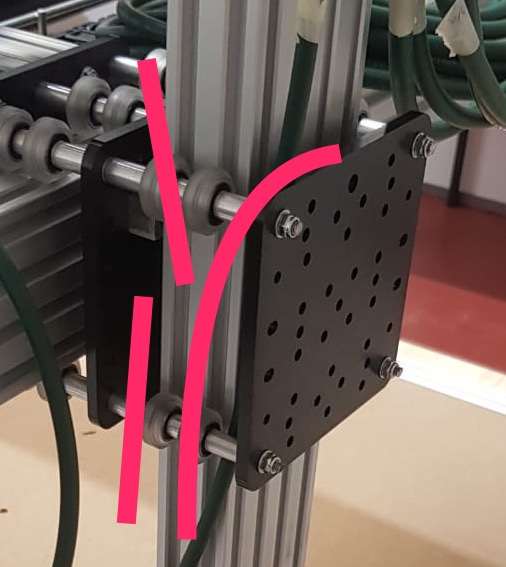
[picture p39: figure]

15

## 6. Issues

### 6.1 Z-Axis bending forward

Figure 15: The Z-axis is bending the rods
As someone is might able to see in the picture, the Z-axis is too heavy. It is bending the 5mm rods. That is the reason, why we decided to add the second Y-axis.

### 6.2 X-Axis not moving

Due to the high load form the Y-axis the wheels running on the X-axis won´t turn. We hope to solve this problem by adding the second gantry plate in order to spread out the weight better and minimize to load on each wheel.

### 6.3 Problems during the construction

- Stainless tubes for the motor mount were to short. You should measure the distance between motor mount and motor with the coupler in-between before cutting of the stainless tubes.
- The screws for the motor mounts are a little bit on the short side, so we had to countersink the holes in the motormounts

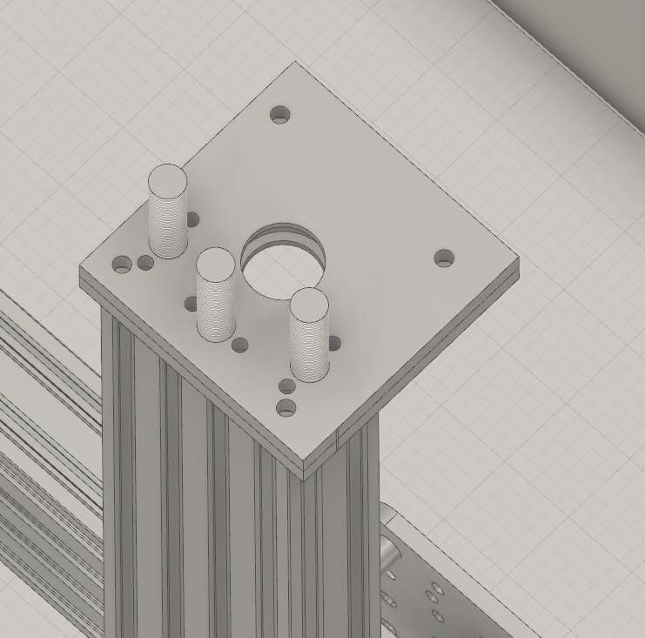
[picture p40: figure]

16

## 7. Update I

In the meantime, while waiting for our C-beams to arrive, we decided to look at the stiffness of the z-axis. It is long, so the risk of it flexing is very high. In order to stiffen up the z-axis we came up with a simple solution. The c-beams allow M12 bolts to be fitted inside their big holes, as shown below:

Figure 16: The z-axis equipped with M12 threaded rods
In this new design, three of the bigger holes in the C-beam are fitted with M12 threaded rods. On both sides spacers will be added and we will carefully tighten up the nuts. The induced tension in the rods should then take sideloads better than the unreinforced C-beam. We hope that this method of inducing pretension in the beam, gives similar results the use of pretension steel in prestressed concrete.³

### 3 https://www.youtube.com/watch?v=P13Mau2VUWw

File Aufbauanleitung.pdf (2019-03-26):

MICRO-MACRO-MINT

# Aufbau der Großformat CNC-Fräse

Sebastian Schütz
17.09.2017

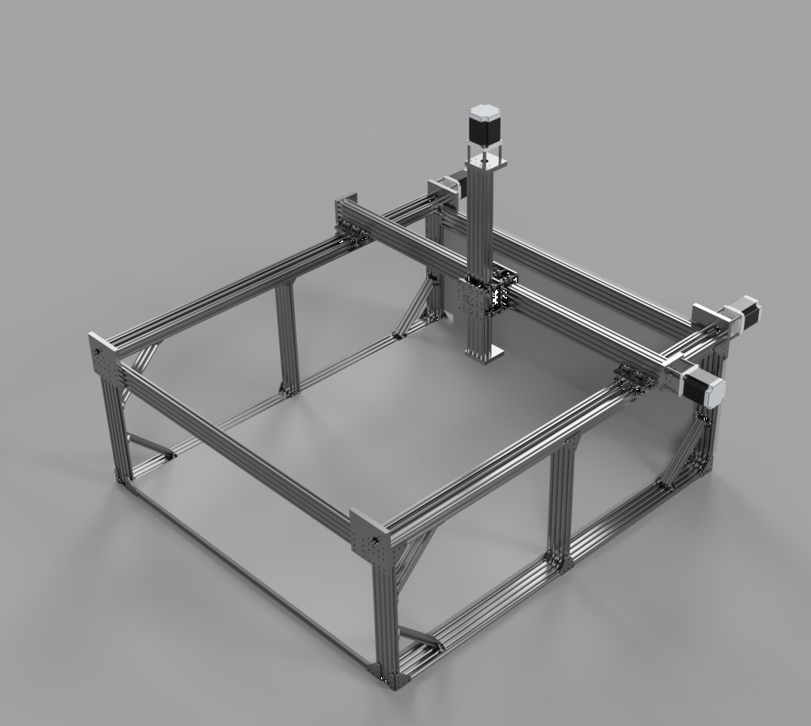
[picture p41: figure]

### Inhalt

## Grundgerüst

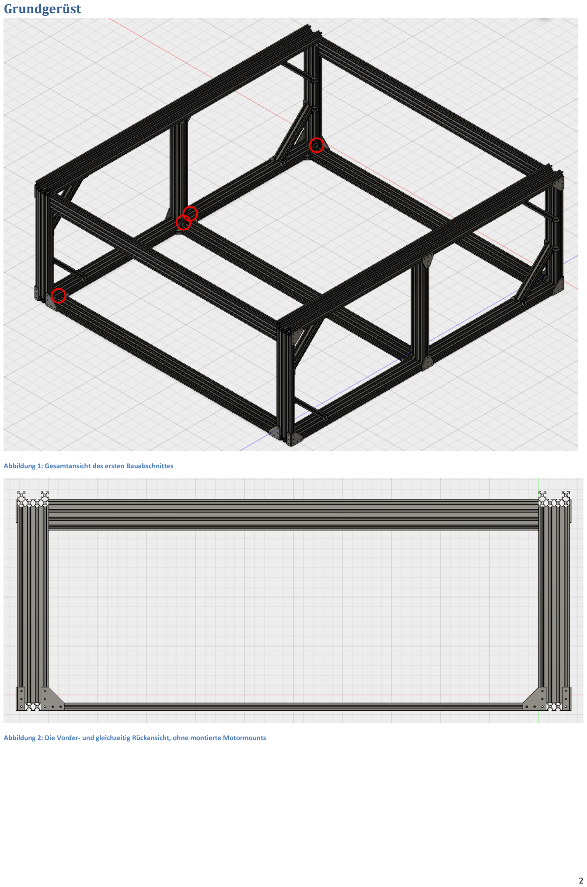
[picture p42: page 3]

Abbildung 1: Gesamtansicht des ersten Bauabschnittes

Abbildung 2: Die Vorder- und gleichzeitig Rückansicht, ohne montierte Motormounts

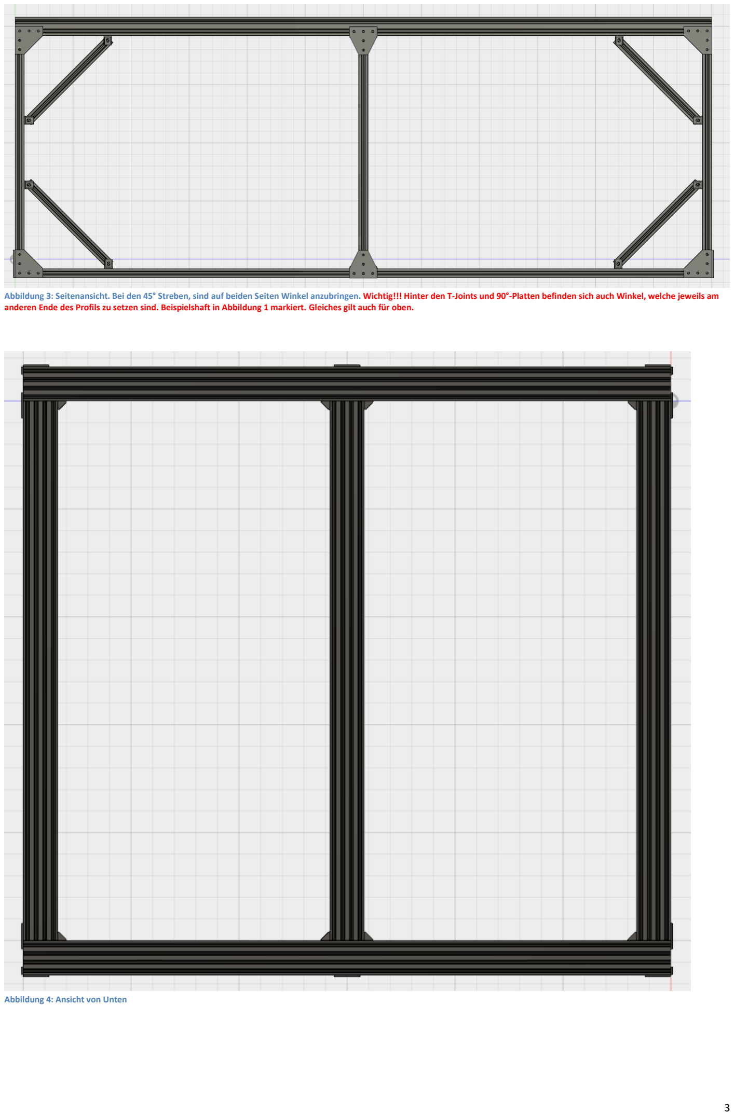
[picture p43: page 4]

Abbildung 3: Seitenansicht. Bei den 45° Streben, sind auf beiden Seiten Winkel anzubringen. Wichtig!!! Hinter den T-Joints und 90°-Platten befinden sich auch Winkel, welche jeweils am anderen Ende des Profils zu setzen sind. Beispielshaft in Abbildung 1 markiert. Gleiches gilt auch für oben.

Abbildung 4: Ansicht von Unten

### Benötigte Materialien

Anzahl | Bezeichnung | Sonstiges
5 | Open-Beam 20x80 – 125 cm | Verbinder der beiden Beine. Müssen in der Schreinerei aus 150cm langen Profilen
| | zugeschnitten werden
2 | Open-Beam 20x80 – 150 cm | Die unteren Profile bei den beiden beinen
6 | Open-Beam 20x80 – 50 cm | Länge messen, müssen alle genau gleich lang sein! Ansonsten in Schreinerei berichtigen

### 2 C-Beam 40x80 – 150 cm

8 | Open-Beam 20x40 – 25 cm | Die 45° Streben. Müssen in der Schreinerei aus 50cm Stücken gesägt werden. Dadurch
| | werden sie ein paar mm kürzer sein, was kein Problem ist. Gegeben falls muss die Ecke,
| | welche zu einem anderen Profil zeigt abgeschliffen werden, damit es passt.
56 | 90° Winkel | 24 sind für die Beine und die Streben die die Beine zusammenhalten (Position in Bildern)
| | 32 sind für die 45° Streben
112 | Schrauben (M5-8mm) und T-Nuts (M5) | 48 für Beine und Streben
| | 64 für 45° Streben
12 | 90 Degree Joining Plate | Je vier pro Bein und zwei vorne und hinten
40 | Schrauben (M5 – 10mm) und T-Nuts (M5) | Acht mal fünf Schrauben bei den Beinen für 90° Platten
16 | Schrauben (M5 – 10mm) und T-Nuts (M5) | Je vier Schrauben für die Platten vorne und hinten
4 | Selftapping Schrauben (M5 – ¾“) | Die je eine selbstschneidende Schraube für vorne und hinten
4 | 3er-Verbinder (3 Hole Joining Strip Plate) | Vorne und hinten zu befestigen. Siehe Bild 2
8 | Schrauben (M5 – 10mm) und T-Nuts (M5) | Je zwei Schrauben pro Verbinder
4 | Selftapping Schrauben (M5 – ¾“) | Die je eine selbstschneidende Schraube für vorne und hinten
4 | T-Verbinder (T Joining Plate) | Für die mittleren Streben. Wie in Bild 3 zu installieren

### 20 Schrauben (M5 – 10mm) und T-Nuts (M5)

### Anmerkungen

- Was zusammengehört (Verbinder und die entsprechenden Schrauben) habe ich der Übersichtlichekeitswillen in der Tabelle mit Rahmen versehen
- Die beiden oberen Streben, welche sich zwischen den beiden C-Beam befinden, können zum jetzigen Zeitpunkt noch nicht befestigt werden. Hierfür
| werden die Motormounts benötigt
- Die fünf Streben, welche sich zwischen den beiden Beinen der CNC-Fräse spannen, werden in der Schreinerei auf der Formatkreissäge auf die passende Länge gesägt. Wenn möglich hierbei auch gleich die MDF-Platte für die Grundfläche zusägen lassen, damit diese die gleiche Länge wie die
| Aluprofile hat.

## Motormounts, Motoren, Schnittplatte und Stabilitätsplatte

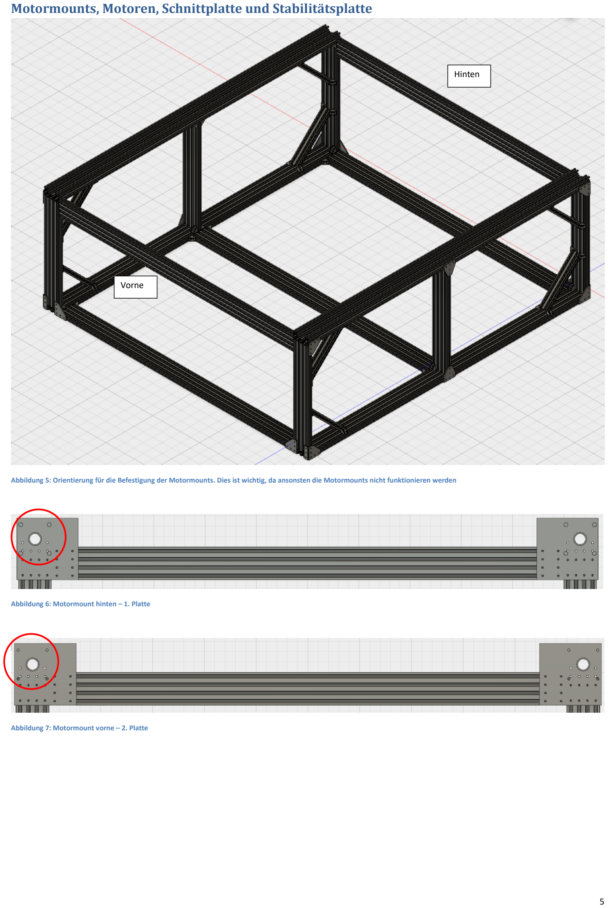
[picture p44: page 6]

Abbildung 5: Orientierung für die Befestigung der Motormounts. Dies ist wichtig, da ansonsten die Motormounts nicht funktionieren werden

Abbildung 6: Motormount hinten – 1. Platte

Abbildung 7: Motormount vorne – 2. Platte

Hinten

Vorne

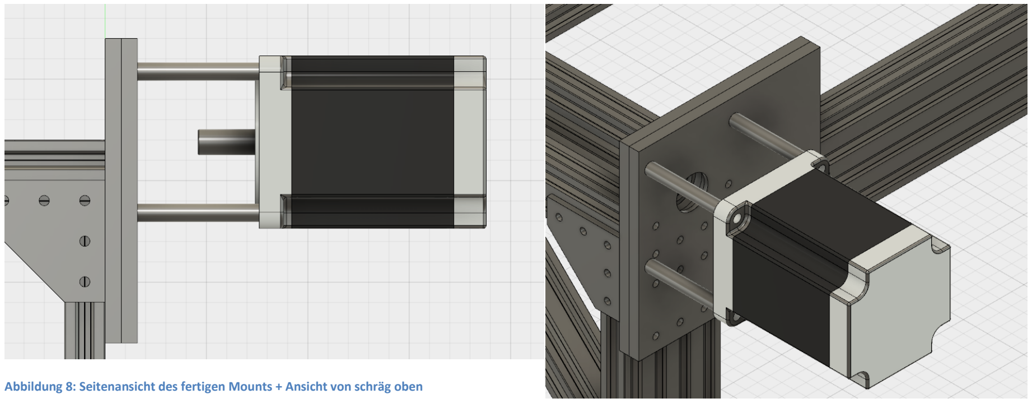
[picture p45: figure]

Abbildung 8: Seitenansicht des fertigen Mounts + Ansicht von schräg oben

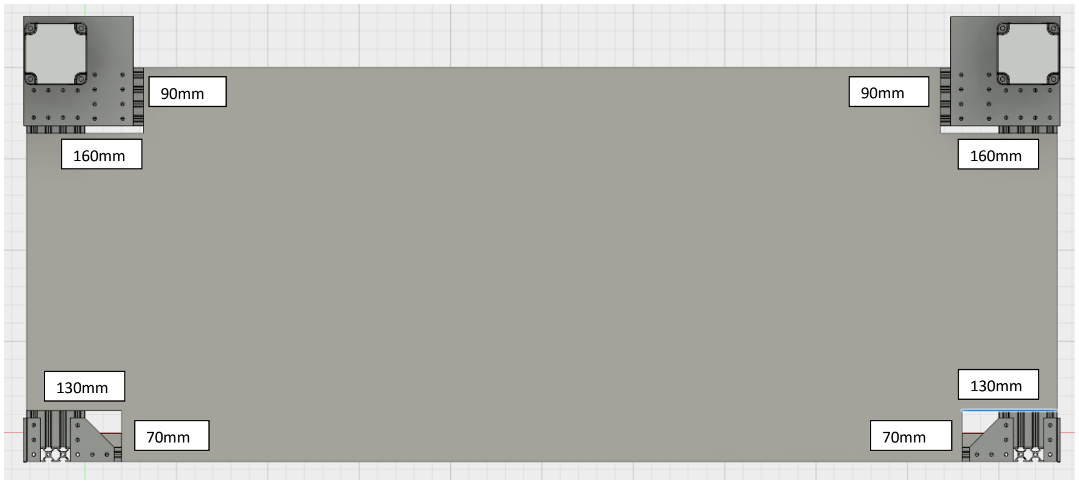
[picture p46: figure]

Abbildung 9: Die Rückplatte mit den Aussparungen

### Benötigte Materialien

Anzahl | Bezeichnung | Sonstiges
8 | Motormountplatten (8mm stark, 15cm x 15cm) | Kriegt ihr, sobald ich sie fräsen konnte. Wäre sinnvoll das Material dafür zuerst zu bestellen,
| | da ich mit Studium nicht weiß, wann ich heim kann/wann ich Zeit dafür finde.
24 | Bohrschrauben (M5 38mm) | Kommen in den C-Beam
64 | Schrauben (M5 – 20mm) und T-Nuts | Jetzt können auch die oberen Streben befestigt werden. Ragt somit 4mm in den Beam. 6mm
| | wären besser, allerdings gibt es keine Schrauben mit 22mm.

### 4 Kugellager 6201

8 | 6 cm Stücke aus Stahlrohr | Unsere Motorhalterung. Genau zuschneiden. Wir dürfen maximal 4cm Verschnitt haben

### 8 M6 100mm Innensechskant + Mutter

2 | NEMA34 Schrittmotoren + Ansteuerung | Bis jetzt keine Verkabelung machen
1 | MDF-Platte 150cm x 125cm – 19mm | Die Schnittplatte. Kann im Notfall auch 15mm stark sein
30 | Schrauben (M5 – 20mm) und T-Nuts | Löcher senken, damit die Schrauben halten und die platte eben ist. Zwischen 4-5mm, aber
| | nicht mehr. Loch entsprechend weit mit größerem Bohrer aufbohren. Die schraube darf
| | maximal 6mm unten hinausragen, ansonsten hält sie nicht.

### 1 OSB-Platte 141cm x 54cm – 19mm

48 | Schrauben (M5 – 25mm) und T-Nuts (M5) | Hier muss nicht gesenkt werden, allerdings brauchen wir auch 19mm stärke

### Anmerkungen

- Wichtig ist die Ausrichtung der Platten. Denkt daran, dass hinten zuerst die Platten befestigt werden müssen, welche eine Aussparung für den Schraubenkopf besitzen, während es vorne die sind, die ein Loch für eine Schraube bei den Motoren besitzen (vgl. Bild 6 und Bild 7)
- Bevor ihr die vorderen Mounts festschraubt, müsst ihr die Beweglichen Schlitten für die X-Achse aufschieben!!!

- Zum Zusammenbau der Mounts:
- Hinten in der zweiten Platte, die Schrauben für die Motoren durchstecken, die Spacer aufstecken und den Motor mit den Muttern befestigen
- Kugellager in dafür vorgesehenes Loch einlassen und die beiden Platten aufeinander pressen. => Lager hierzu vielleicht zuvor in den Eisschrank, damit es sich ein bisschen zusammenzieht und leichter hineinpasst. Es wird sehr eng werden. Nicht mit einem Hammer darauf schlagen. Wenn dann Holzbrett und Gummihammer.
- Platten mit Schrauben festschrauben. Wird eine Fummelei. (Ratsche??) Teilweise sehr wenig Platz mit den Schraubenköpfen => Spacer entsprechend Schräg anschleifen, dass sie Platz finden, aber dabei den Spacer nicht kürzen!!
- Die Schnittplatte mit je 10 Schrauben pro Querstrebe befestigen. In an die inneren und äußeren Schienen ranschrauben.
- Bei der Stabilitätsplatte jeweils 8 Schrauben und Mutternpaare in die langen Seiten (=> 32 Schrauben insgesamt) und je 4 Schrauben und Mutternpaare in die kurzen Seiten

## Installation der beweglichen Teile

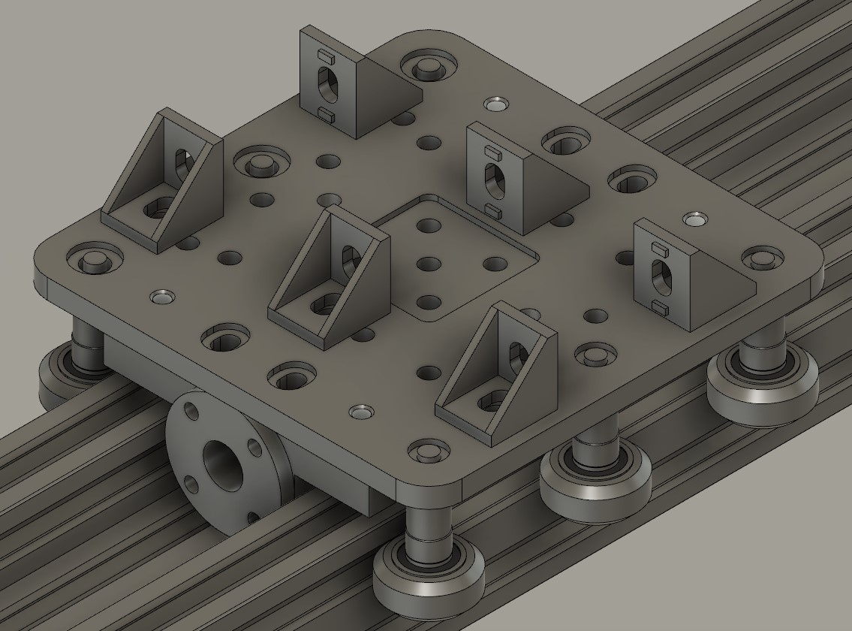
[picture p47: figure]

Abbildung 10: Großansicht des beweglichen Schlittens

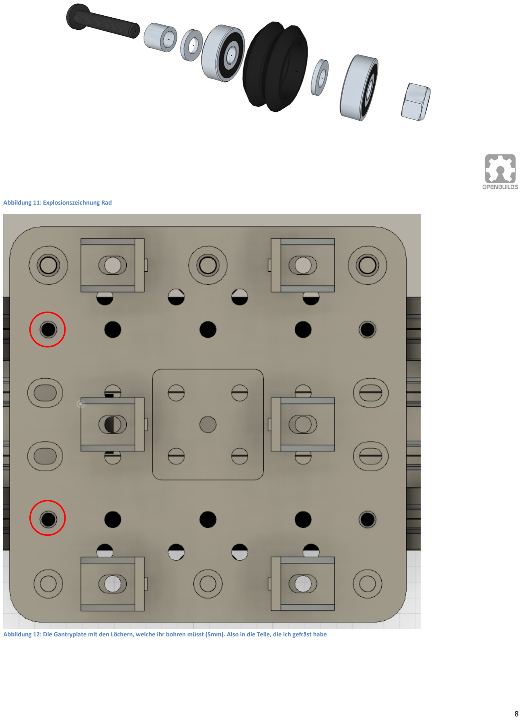
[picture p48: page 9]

Abbildung 11: Explosionszeichnung Rad

Abbildung 12: Die Gantryplate mit den Löchern, welche ihr bohren müsst (5mm). Also in die Teile, die ich gefräst habe

### Benötigte Materialien

Anzahl | Bezeichnung | Sonstiges

### 2 C-Beam Gantry Plate Xlarge 2 Anti Backlash Nuts

8 | Schrauben (M4 – 25mm) und Muttern | Zur Befestigung der Anti Backlash Nuts
2 | Aluteile 15 mm dick | Daraus fräße ich die Halterung
4 | Schrauben (M5 – 25mm) und Muttern | Flacher Kopf!!! Und ihr müsst die Befestigungslöcher selber Bohren. Siehe Bild 12
12 | Wheel Sets | Im Set sind: Rad, 2 Kugellager, 2 Beilagscheiben, 1 Mutter
12 20 mm Spacer

### 12 Schrauben (M5 – 45mm)

12 90° Winkel für Y-Achse
12 | Schrauben (M5 – 8mm) und T-Nuts | Zur Befestigung des C-Beams der Später die Y-Achse darstellt

### 12 Schrauben (M5 – 15 mm) und Muttern mit

| Selbstsicherung | Zur Befestigung an der Platte

### 2 TR12-3 Gewindestangen 160 cm 8 TR12-3 Muttern 8 Madenschrauben (M3 – 4mm) 2 Coupler 12mm-14mm

### Anmerkungen

- Befestigt die Räder so, dass der Schraubenkopf auf der Oberseite der Platte ist und die Mutter unten.
- Erst die Räder, dann die Mutter für die Gewindestange, dann die Gewindestangen reinschieben und drehen => mit dem Coupler mit dem Motor verbinden => im Vorfeld die Messingmuttern samt Madenschraube aufdrehen. Wenn mit Coupler verbunden, handfest andrehen, sodass es das Kugellager einquetscht und mit Madenschraube fixieren
- Ihr müsst die Löcher für die Madenschrauben selber bohren und mit einem Gewinde versehen!

## Y-Achse

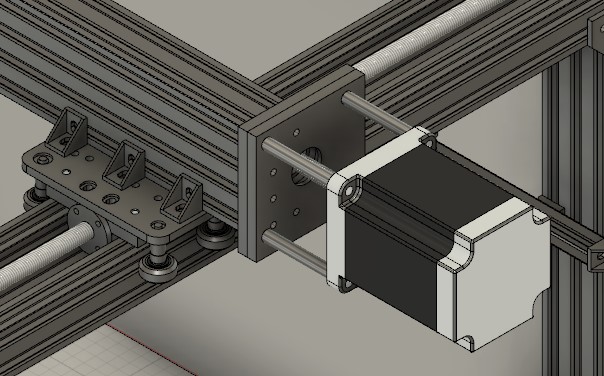
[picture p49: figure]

Abbildung 13: Motormount Y-Achse. Zusammenbau wie zuvor. Auch auf Spiegelung auf der anderen Seite achten

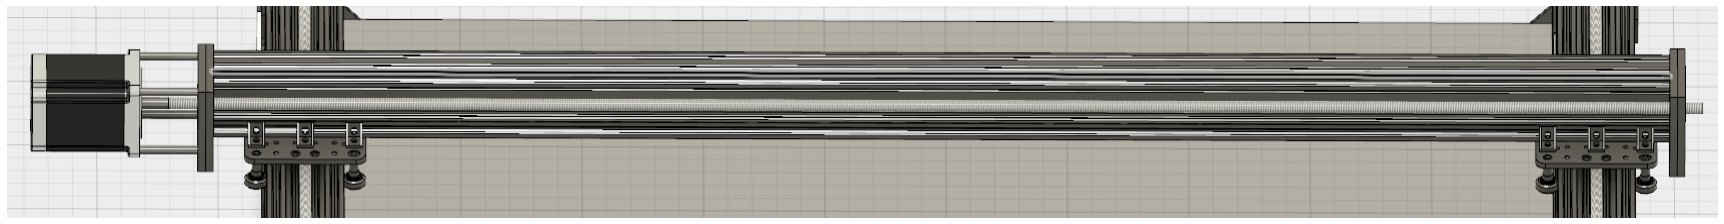
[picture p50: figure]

Abbildung 14: Ansicht der Y-Achse von hinten

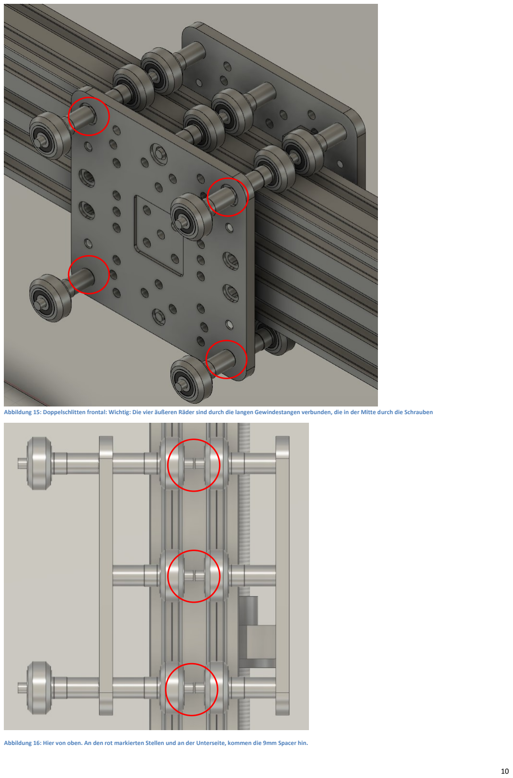
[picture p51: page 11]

Abbildung 15: Doppelschlitten frontal: Wichtig: Die vier äußeren Räder sind durch die langen Gewindestangen verbunden, die in der Mitte durch die Schrauben

Abbildung 16: Hier von oben. An den rot markierten Stellen und an der Unterseite, kommen die 9mm Spacer hin.

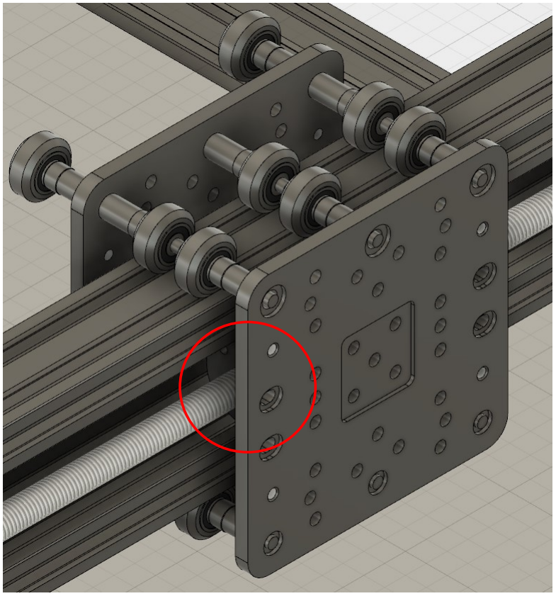
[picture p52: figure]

Abbildung 17: Doppelschlitten. Auch hier muss die Antibacklashnut mit dem Halter befestigt werden und die Löcher gebohrt werden.

### Benötigte Materialien

Anzahl | Bezeichnung | Sonstiges
1 | C-Beam 40x80 – 150 cm | Befestigung und Ausrichtung wie im Bild

### 1 TR12-3 Gewindestange 160 cm 4 TR12-3 Muttern 4 Madenschrauben (M3 – 4mm) 1 Coupler 12mm-14mm 4 Motormountplatten (95mm x 95mm 8mm

| stark) | Sind nicht die gleichen wie die für die Z-Achse!!! Unterscheiden sich um einen zehntel mm bei
| | der Lochausrichtung, was später Spannung auf die Gewindestange bringen würde und einen
| | unruhigen Lauf provoziert!!! Also nicht vertauschen

### 2 Kugellager 6201 12 Bohrschrauben (M5 38mm) 1 NEMA34 Schrittmotoren + Ansteuerung

4 | 6 cm Stücke aus Stahlrohr | Unsere Motorhalterung. Genau zuschneiden. Wir dürfen maximal 4cm Verschnitt haben

### 4 M6 100mm Innensechskant + Mutter

16 | Wheel Sets | Im Set sind: Rad, 2 Kugellager, 2 Beilagscheiben, 1 Mutter
16 20 mm Spacer

### 2 C-Beam Gantry Plate Xlarge

6 | 9mm Spacer mit 5mm Innendurchmesser | Kommen zwischen die Räder, die den C-Beam „umfassen“
4 | M5-Gewindestange – 20cm | Für die vier Ecken
8 | Sicherheitsmuttern (M5) | für oben genannte Gewindestange
2 | M5-Gewindestange – 10cm | für die Räder in der Mitte
2 | Sicherheitsmuttern (M5) | Für die Schrauben

### 1 Anti Backlash Nuts

4 | Schrauben (M4 – 25mm) und Muttern | Zur Befestigung der Anti Backlash Nuts
1 | Aluteile 15 mm dick | Daraus fräße ich die Halterung
2 | Schrauben (M5 – 25mm) und Muttern | Flacher Kopf!!! Und ihr müsst die Befestigungslöcher selber Bohren. Siehe Bild 17
8 | Präzisionsbeilagscheiben (1mm) | immer 2 kommen in die in Abbildung 15 markierten Löcher. Ja, die kommen da zusätzlich hin

### Anmerkungen

- Der Aufbau der Mounts funktioniert genau gleich wie zuvor, lediglich eine andere Form
- Der Doppelschlitten ist hier der schwierige Part. Die Bilder sind aber glaube ich recht hilfreich

## Z-Achse

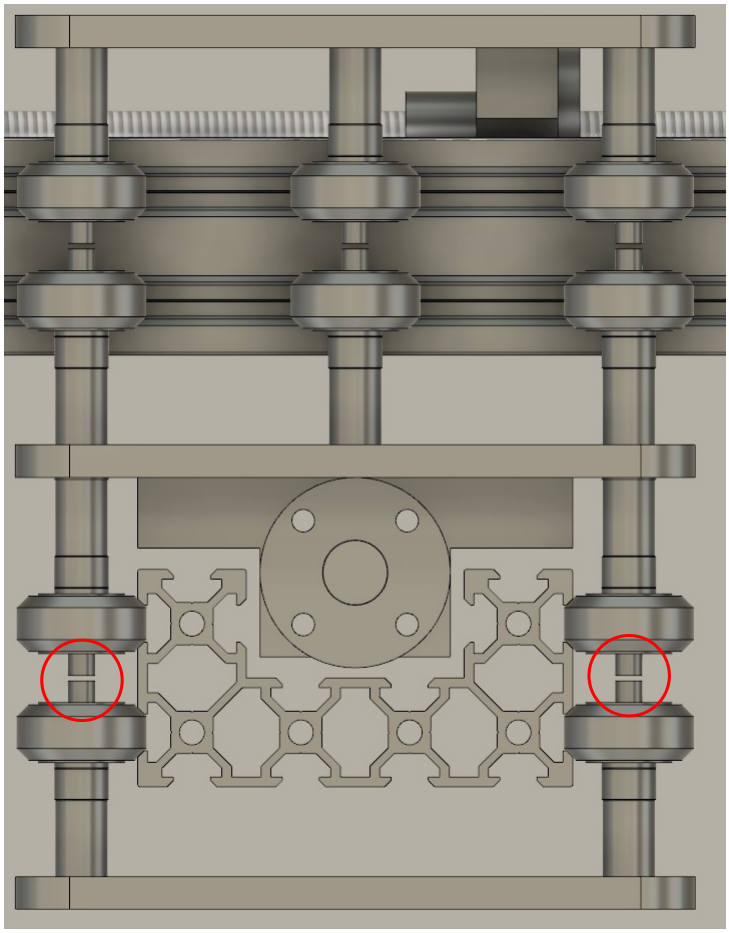
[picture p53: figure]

Abbildung 18: Fertige Ansicht. An den roten Stellen, wieder 9mm Spacer

Abbildung 19: Ansicht von oben

### Benötigte Materialien

Anzahl | Bezeichnung | Sonstiges
1 | C-Beam 70cm | Muss aus einem 1m Stück geschnitten werden. Schreinerei
1 | TR12-3 Gewindestange ~78 cm | Ein Stück mit 80cm wurde bestellt. Kann nach einbau gekürzt werden.

### 1 Anti Backlash Nut

4 | Schrauben (M4 – 25mm) und Muttern | Zur Befestigung der Anti Backlash Nuts
1 | Aluteile 15 mm dick | Daraus fräße ich die Halterung
2 | Schrauben (M5 – 25mm) und Muttern | Flacher Kopf!!! Und ihr müsst die Befestigungslöcher selber Bohren.
4 | Wheel Sets | Im Set sind: Rad, 2 Kugellager, 2 Beilagscheiben, 1 Mutter
4 20 mm Spacer

### 1 C-Beam Gantry Plate Xlarge

4 | 9mm Spacer mit 5mm Innendurchmesser | Kommen zwischen die Räder, die den C-Beam „umfassen“

### 1 Coupler 12mm-14mm 4 Motormountplatten (95mm x 95mm 8mm

| stark) | Sind nicht die gleichen wie die für die Y-Achse!!! Unterscheiden sich um einen zehntel mm bei
| | der Lochausrichtung, was später Spannung auf die Gewindestange bringen würde und einen
| | unruhigen Lauf provoziert!!! Also nicht vertauschen

### 2 Kugellager 6201 12 Bohrschrauben (M5 38mm) 1 NEMA34 Schrittmotoren + Ansteuerung 4 M6 60mm Spacer/Stahlrohr mit 6,5-7mm

| Innendurchmesser

### 4 M6 100mm Innensechskant + Mutter 4 TR12-3 Muttern 4 Madenschrauben (M3 – 4mm)

### Anmerkungen

- Das montieren der Z-Achse wird schwierig. Überlegt euch zuerst, wie ihr das ganze zusammensetzt, sonst baut ihr die Gewindestange fünf Mal ein und aus, bis ihr alles zusammen habt.

## Weiteres

Es gibt jetzt noch eine ganz Reihe an Dingen, die nach diesem Aufbau noch fehlen/erledigt werden müssen:

- Befestigung eines Spindelmounts
- Endschalter
- Kabel verlegen und allgemein die Verdrahtung
- Die Montage des 3D-Druckkopfes
- Fetten der Gewindestangen => Wichtig wegen Rost und natürlich Abrieb
- Inbetriebnahme und Kalibrierung
- …

Achtet beim Bau auf einen ebenen Untergrund und die genaue Ausrichtung der Teile. Nehmt einen 90° Winkel zur Hand, damit die 90° tatsächlich 90° werden und messt über die Diagonalen, um dann noch einmal nachbessern zu können. Durch die Schnittplatte und die Rückplatte können wir auch ein bisschen was ziehen. Schnitte bitte nie mit der Hand und auch die Bohrungen (nicht die für die Rückplatte und Bodenplatte) an der Säulenbohrmaschine machen!!!

Schrauben und Muttern sind im Modell der Einfachheit halber nicht eingezeichnet. Daran auch denken nicht, dass man sie dort sucht.

Modell verfügbar unter: http://a360.co/2y7nwAO

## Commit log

2019-03-20 Motormountfiles as 3D DXF
    [Bein links - Motormount hinten I.dxf, Bein links - Motormount hinten II.dxf, Bein rechts - Motormount hinten I.dxf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]
2019-07-12 The circuit diagram
